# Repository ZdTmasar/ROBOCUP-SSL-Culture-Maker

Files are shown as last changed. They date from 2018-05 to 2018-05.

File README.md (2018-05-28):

# ROBOCUP-SSL-Culture-Maker
This is the work of LOO Darren, LAKHAL Nada, SEHOUBO Victoire and SALIBA Thomas for Rhoban SSL team

You will find a report on the repository explaining everything done during the project.

Basically there is :
-> How to make an identification of a motor
-> How to calculate a PID corrector
-> How to implemente the corrector
-> How to build a TestBench for a motor

If you are intersted in the SSL and more particularly with Rhoban, be sure to contact them. The remaining of the code is with them !

If you have any problem or questions about our work, be sure to contact us ;)

You will find the work of LAKHAL Nada and  SEHOUBO Victoire at the following google drive :

https://drive.google.com/drive/folders/1fRvp3v9pUFU8v6p59sLrBkBSSc9Q6jl7?usp=sharing

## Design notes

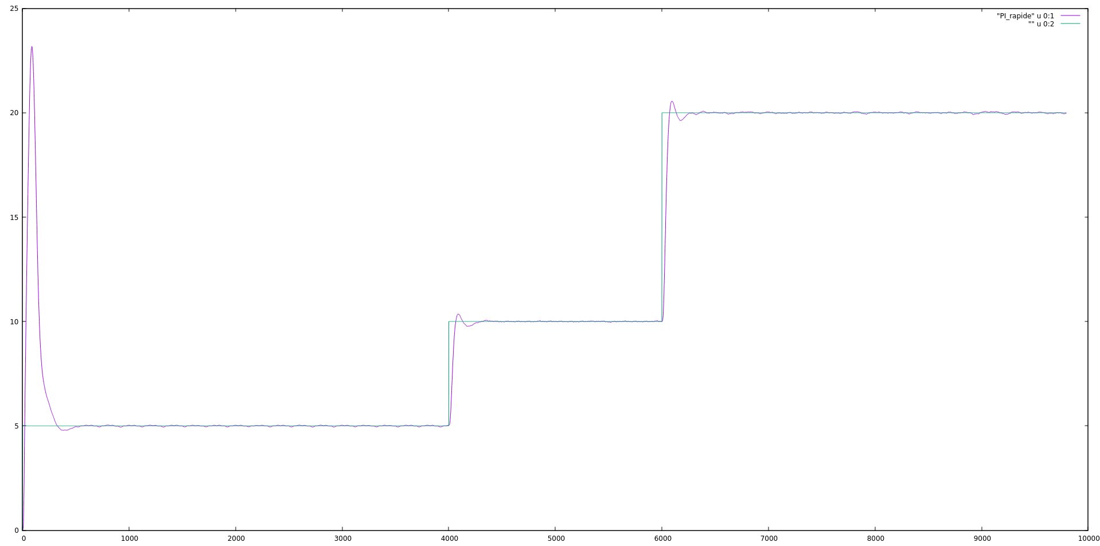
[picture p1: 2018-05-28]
Curves/Pi_rapide.png

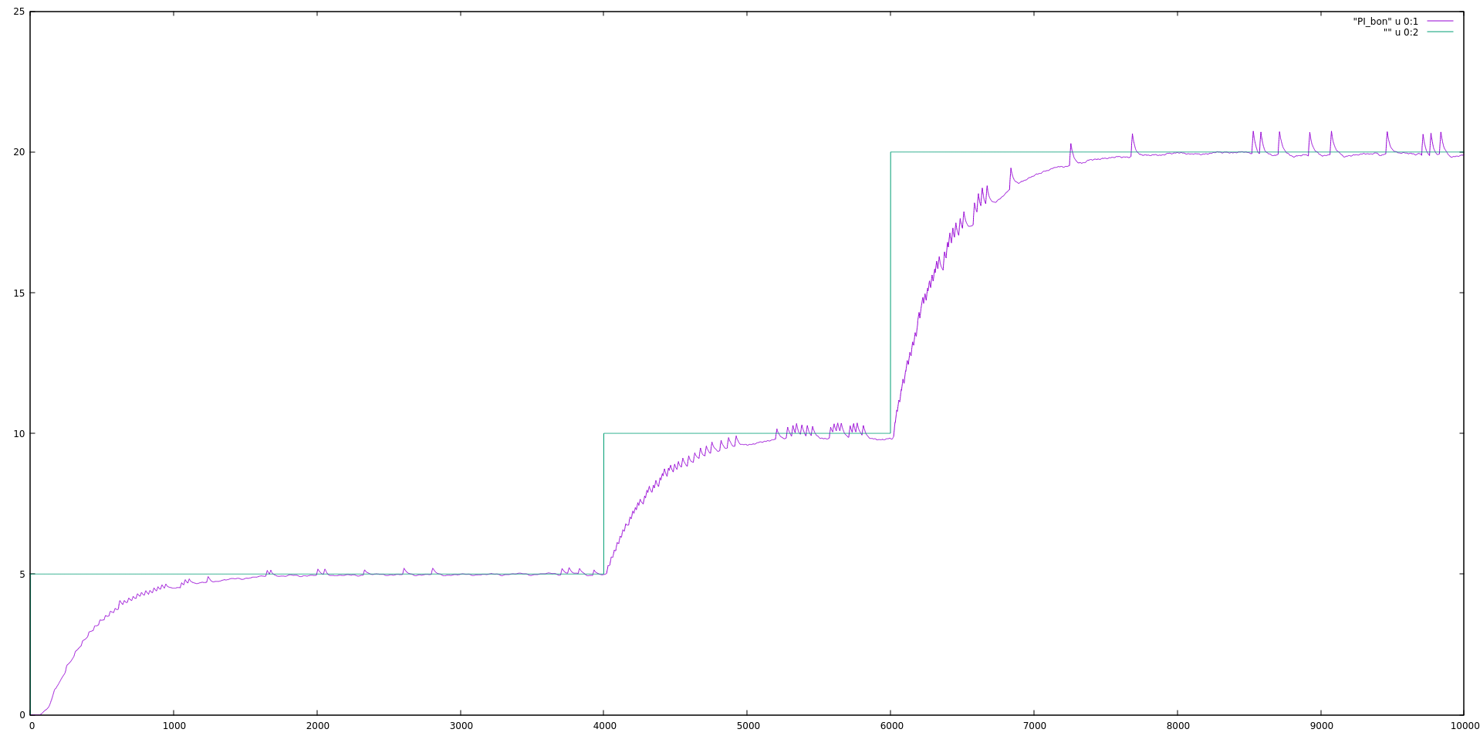
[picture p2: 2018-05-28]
Curves/PI_bon_arrache.png

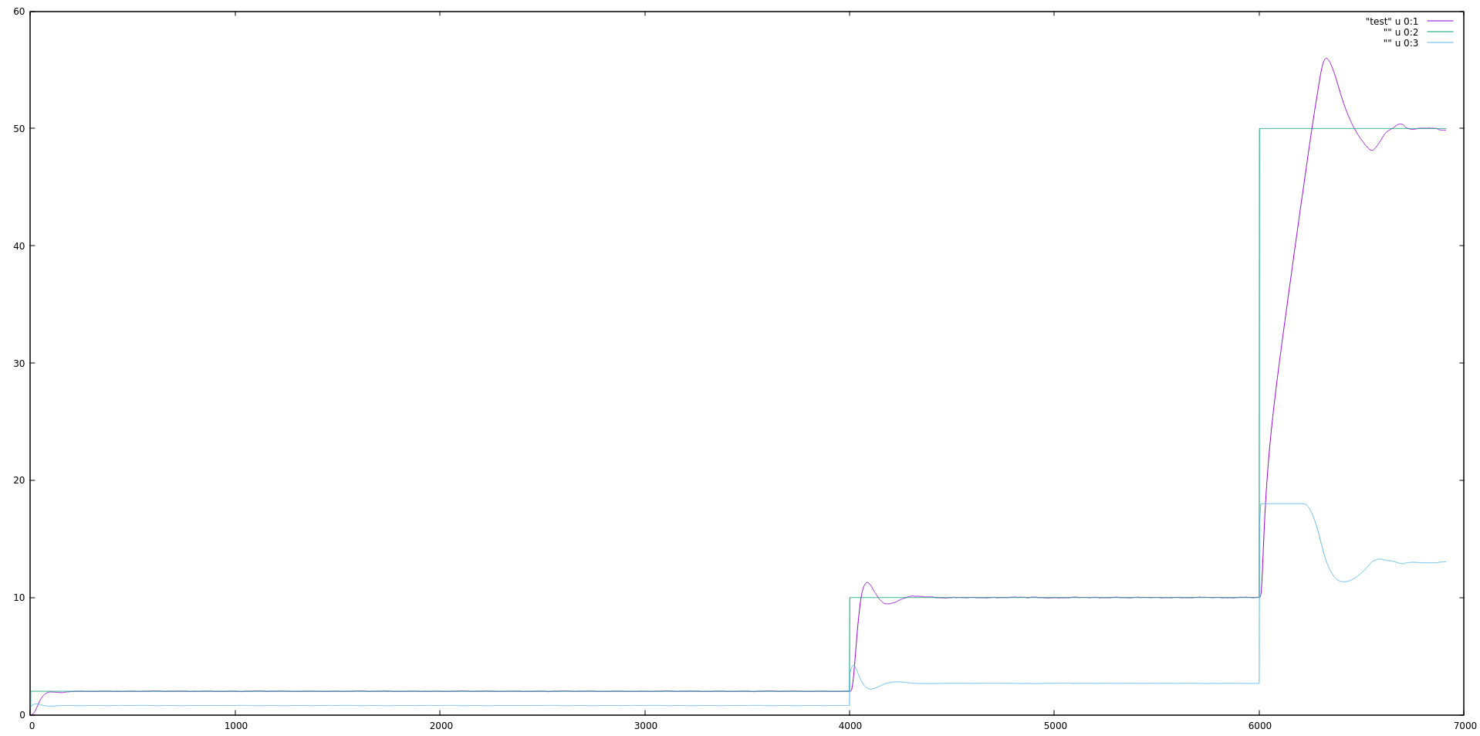
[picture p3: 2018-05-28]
Curves/PI_piffé_0.0536_-0.523.png

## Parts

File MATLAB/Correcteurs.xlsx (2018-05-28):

Ordre Procédé | Correcteur | wu | wi | Tr5% | 1er Dépassement | Coefficient Commande | Coefficient Erreur | Date | Commentaire | Tension moteur
2 | FPI | 20 | wu | 0,165 s | 8.75% | [1] | [0,0512; -0,0502] | 2018-04-13 | Pas trop mal mais plus lent que FPI2 | 20V
2 | FPI2 | 20 | wu | 0,163 s | 5% | [1] | [0,0524; -0,0514] | 2018-04-13 | Pas trop mal | 20V
1 | Caca | 20 | wu/2 | 0,408 s | 0 | [1] | [0,0356; -0,0352] | 2018-04-27 | Peut-être un peu trop lent | 20V
2 | Caca2 | 20 | wu/2 | 0,290 s | 0 | [1] | [0,0660; -0,0653] | 2018-04-27 | On a des possibilités | 20V
1 | Moto1 | 20 | 1,5*wu | 0,176 s | 6.25% | [1] | [0.0223; -0.0216] | 2018-04-27 | Un peu petit | 20V
2 | Moto2 | 20 | 1,5*wu |  |  | [1] | [0.0413; -0.0401] | 2018-04-27
1 | Moto1 Co+ | 20 | 1,5*wu |  |  | [1] | [0.0254; -0.0246] | 2018-04-27
 | A la main |  | 0,223 s | 16.25% | [1] | [0,0536; -0,0523] | 2018-05-03 | Plus lent que FPI et double dépassement | 24V
1 | Moto1 Co++ = 0,0440 | 20 | wu |  |  | [1] | [0.0444; -0.0436] | 2018-05-03
 |  |  |  |  | [1 -2.8971 2.7950 -0.8979] | [0.0014 -0.0013 -0.0014 0.0013]

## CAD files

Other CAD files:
TestBench_Inventor/Aimant_tenir.ipt
TestBench_Inventor/Brushless_70W.ipt
TestBench_Inventor/OldVersions/Aimant_tenir.0001.ipt
TestBench_Inventor/OldVersions/Brushless_70W.0001.ipt
TestBench_Inventor/OldVersions/Socle_Testbench.0006.ipt
TestBench_Inventor/OldVersions/Support_Carte.0017.ipt
TestBench_Inventor/OldVersions/Support_carte_ground.0003.ipt
TestBench_Inventor/OldVersions/Support_motor_front.0009.ipt
TestBench_Inventor/OldVersions/Support_motor_front_2.0001.ipt
TestBench_Inventor/OldVersions/Support_motor_front_ground.0007.ipt
TestBench_Inventor/OldVersions/TestBench.0009.iam
TestBench_Inventor/Socle_Testbench.ipt
TestBench_Inventor/Support_Carte.ipt
TestBench_Inventor/Support_carte_ground.ipt
TestBench_Inventor/Support_motor_back.ipt
TestBench_Inventor/Support_motor_front.ipt
TestBench_Inventor/Support_motor_front_2.ipt
TestBench_Inventor/Support_motor_front_ground.ipt
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

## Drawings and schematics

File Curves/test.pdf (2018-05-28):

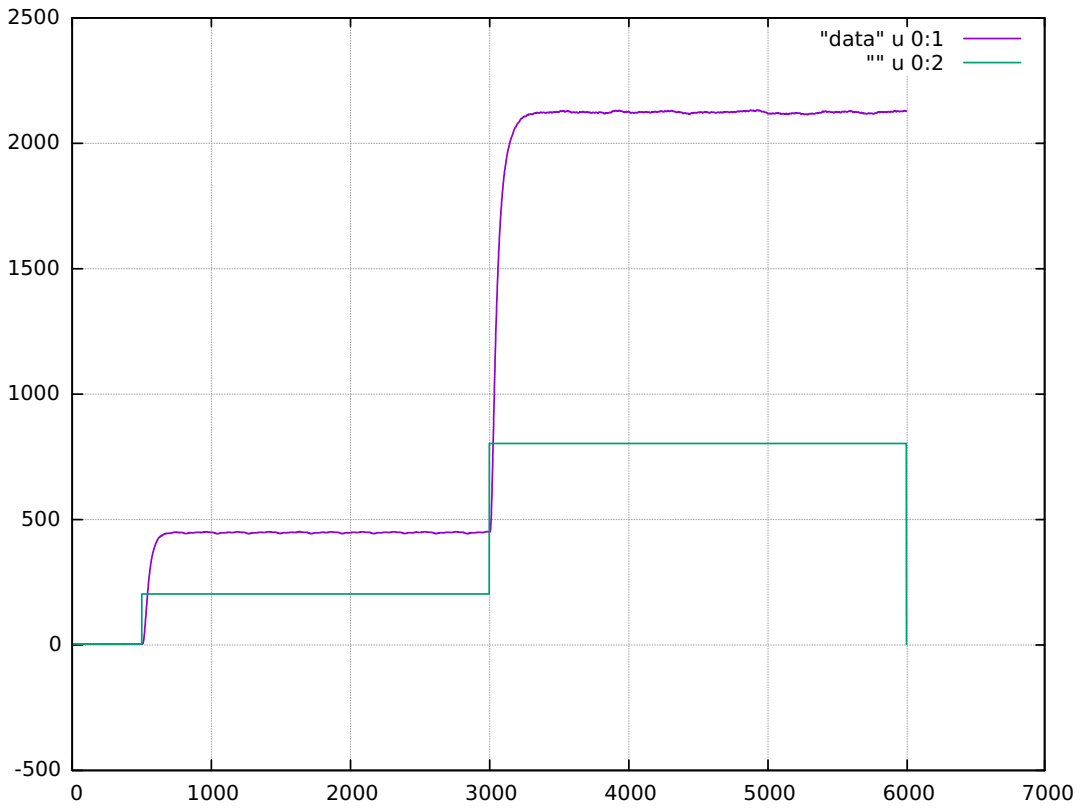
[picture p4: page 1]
"data" u 0:1 "" u 0:2

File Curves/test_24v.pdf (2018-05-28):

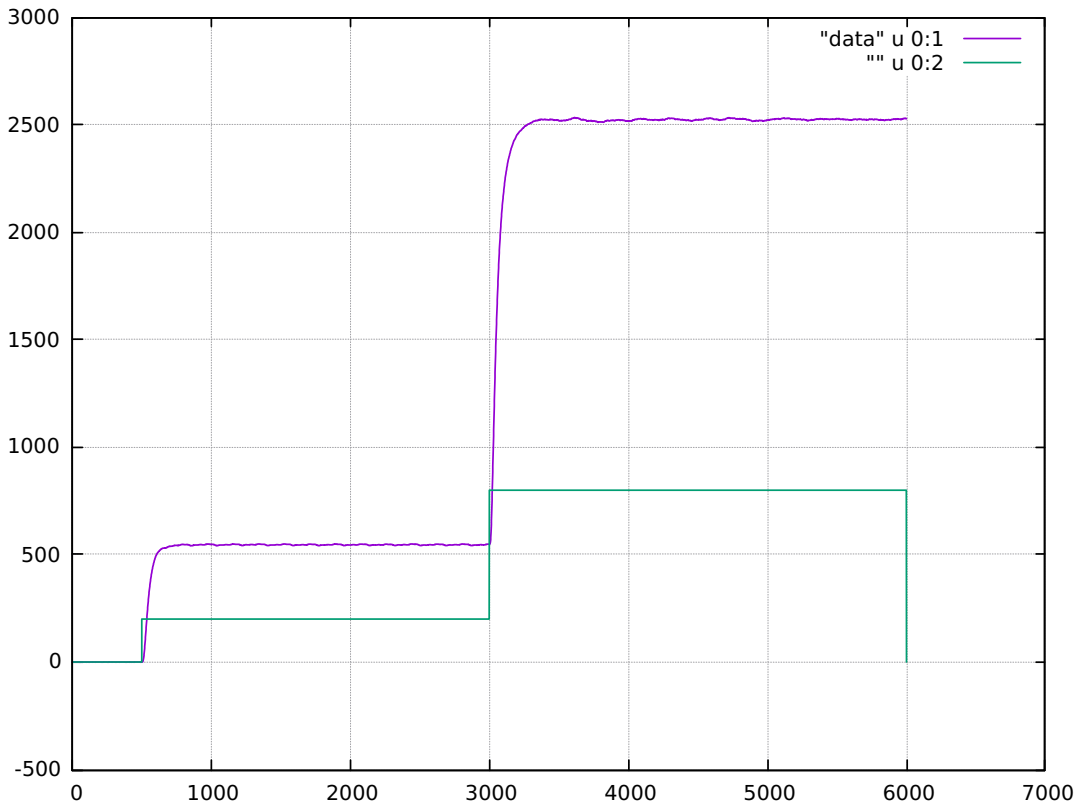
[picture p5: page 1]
"data" u 0:1 "" u 0:2

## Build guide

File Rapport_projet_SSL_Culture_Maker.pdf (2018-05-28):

# ROBOCUP SSL

## - PREMISSES A L’ASSERVISSEMENT D’UN ROBOT HOLONOME -

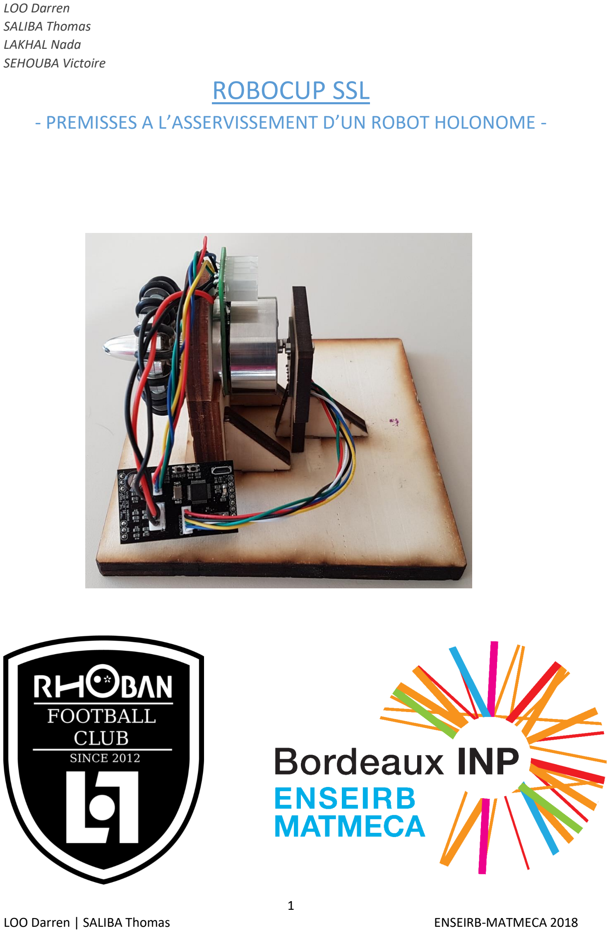
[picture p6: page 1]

LOO Darren | SALIBA Thomas | ENSEIRB-MATMECA 2018

LOO Darren
SALIBA Thomas
LAKHAL Nada
SEHOUBA Victoire

## SOMMAIRE

## Contexte

La Robocup est l’une des compétitions de robotique la plus connue dans le monde. Elle regroupe plusieurs catégories : Robocup Soccer (SSL, MSL, Humanoid, etc..), Robocup Rescue, Robocup @Home, Robocup Industrial et Robocup Junior. La catégorie qui nous intéresse ici est la SSL (Small Size League) de la Robocup Soccer.
Le principe est de se faire affronter deux équipes de six robots à roues qui sont pour la plupart holonomes dans un match de football. Les défis sont donc d’arriver à faire un robot maniable, précis et rapide mais sans qu’il soit incontrôlable. L’objectif de ce livret est de démarrer l’implémentation d’un asservissement d’un robot SSL par une approche rigoureuse et méthodologique de l’automatique. Ce livret contient donc les parties suivantes :
➔ Décomposition du robot
➔ Création d’un TestBench
➔ Identification d’un moteur seul
➔ Asservissement d’un moteur seul ➔ Identification d’un moteur in situ
➔ Asservissement d’un moteur in situ

Chaque partie sera introduite et expliquée de manière simple et didactique. Cependant certaines explications seront succinctes car il existe des documents qui approfondissent beaucoup mieux le propos (Voir Bibliographie pour plus de détails). L’étude se fera sur un robot holonome de l’équipe Rhoban utilisant 4 moteurs brushless Maxon EC 45 flat en Direct Driving.

## Décomposition du robot

Pour contrôler parfaitement un robot, il faut le connaître, c’est-à-dire identifier son comportement par rapport à certaines commandes. Cette phase, l’identification, doit être faite plusieurs fois à différents niveaux : une roue, toutes les roues ensemble puis le robot entier.
Dans un premier temps, il est nécessaire de pouvoir contrôler correctement chaque moteur. Pour cela, il faut effectuer une identification du moteur : il faut caractériser son comportement et sa réponse à une commande. Pour cela, un banc de test a été conçu pour accueillir un moteur et effectuer des tests plus facilement. Dans cette première version, le moteur tourne avec une roue holonome : il n’y a que la charge de la roue sur l’axe du moteur.
Une fois que le moteur a été identifié, que son comportement a été caractérisé, que son modèle de comportement a été établi, il devient possible de synthétiser un correcteur qui permettra d’obtenir du moteur une vitesse souhaitée et ce quel que soit les perturbations. On obtient donc la chaine suivante :

Figure 1 : Schéma bloc d’une chaîne asservie

G représentant le comportement du moteur sous forme de fonction de transfert (vitesse de rotation/tension appliquée), et C le correcteur que l’on synthétisera par la suite. Il est à noter que le retour sur la vitesse de la roue provient d’un encodeur magnétique captant le champ tournant d’un aimant fixé à l’arrière du moteur brushless.
Une fois cette chaîne implémentée et validée, on peut se concentrer sur un autre banc de test qui met en situation le moteur avec un certain poids appliqué en sa surface. L’idée est de refaire l’identification du moteur avec les contraintes qu’il aurait sur le robot. La chaine précédente est surtout pour valider tous les éléments nécessaires : le capteur, le calcul, l’implémentation. Car une fois tout ceci validé, refaire une identification et la mettre en place est très simple.
Maintenant, chaque processus va être détaillé.

## Conception du premier banc de test

Il y a plusieurs manières d’effectuer un banc de test. Ce qui sera décrit par la suite se rapproche de ce qui a semblé être le plus simple à mettre en œuvre.
Les contraintes qui ont été fixées sont les suivantes :
-le moteur doit être soutenu dans son intégralité ;
-la roue ne doit pas toucher le sol ;
-l’ensemble doit être stable lors des tests ;
-il faut que l’encodeur magnétique soit parfaitement en vis-à-vis de l’aimant.
En effet, il faut un maximum de stabilité pour éviter que des perturbations viennent altérer les mesures. Le placement de l’encodeur magnétique est très important car c’est lui qui effectue les mesures sur lesquelles tout l’asservissement se base.
Globalement, le banc de test est composé de 5 pièces différentes. Toutes les pièces ont été conçues avec le logiciel Autodesk Inventor et ont été faite par découpage laser sur bois.

### Concevoir une pièce

La conception d’une pièce est séquentielle. En effet, on ne peut généralement travailler que sur une surface à la fois. Il faut donc avoir une bonne idée des objectifs que la pièce devra remplir. Des ébauches au crayon sont toujours un bon début. Dans notre cas, puisque les pièces seront faîtes par découpage laser, il n’y aura qu’une face à faire. Toutefois, la démarche peut être réitérée autant de fois que possible pour effectuer des pièces plus compliquées. Dans tous les cas, il faut toujours garder à l’esprit le moyen qui sera utilisé pour fabriquer la pièce (découpage, impression 3D, pliage, emboutissage, usinage etc…), certaines formes étant impossible à réaliser selon le procédé d’usinage retenu.
Dans notre cas, les 5 pièces sont :
- le socle du banc de test ;
- un support pour le moteur ;
- un support pour la carte de l’encodeur ;
- des soutiens pour les supports (2 identiques pour le moteur et 1 pour la carte) ;

### Dessiner une face

Pour dessiner une face plane, il faut créer une esquisse. Dans un premier temps, dans le volet de navigation du modèle, sélectionner un plan qui servira de référence à l’esquisse. Puis créer une esquisse. Le logiciel propose plusieurs fonctions qui permettent de créer des formes géométriques simples. L’outil « Ajuster » (icône de ciseaux) permet de supprimer des portions de trait non désirées. Pour fixer des éléments par rapport à d’autres, il faut utiliser des contraintes. Il y a plusieurs types de contraintes : de dimensions (qu’on appelle des côtes), de positionnement (coïncidence de points, colinéarités d’axes ou parallélisme…). Lorsqu’un élément est totalement contraint, il apparaît en bleu sur l’esquisse, les éléments non contraints étant en vert. Contraindre totalement une esquisse a plusieurs avantages. Dans un premier temps, cela permet de maîtriser totalement les dimensions / orientations que prendra la pièce. De plus, si une esquisse est bien contrainte, il est aisé d’en changer les dimensions sans que cela ait d’impact néfaste sur tout le travail qui sera effectué après et qui se base sur l’esquisse même. Aussi, cela permet à un tiers de voir clairement les relations qu’il peut y avoir entre les éléments ne laissant plus aucune place au doute.
Enfin, une fois que l’esquisse est réalisée et prête, il est possible de l’extruder : de l’utiliser pour créer de la matière ou encore de l’utiliser pour enlever de la matière (sur une pièce déjà existante par exemple). Dans notre cas, une extrusion de 10mm a été effectuée sur toutes les pièces. En effet, les planches de bois qui passeront au découpage sont d’épaisseur 10mm.

### Assembler les pièces

Une fois que toutes les pièces ont été réalisées, il est possible de les assembler afin d’avoir un bon aperçu du montage final.
Il faut créer un fichier de type « Ensemble » et y placer les différentes pièces qui ont été faites. Pour des raisons pratiques, il est préférable de commencer par la pièce centrale du montage. Puis, il faut bloquer la pièce dans l’espace pour inhiber ses déplacements. Ensuite il faut rajouter les autres pièces. Pour placer une pièce, il faut aussi lui imposer des contraintes, de position (distance, colinéarité…) et de surface (placage en vis-à-vis ou affleurement etc…).
Pour qu’une pièce fixe soit bien contrainte, il faut lui retirer ses 6 degrés de liberté dans l’espace (3 translations sur les axes du repère et 3 rotations autour de ces axes). Si une pièce est mobile, il faut bien sûr lui laisser les degrés de liberté nécessaires.
Afin de vérifier qu’un assemblage se passe sans accroc, il est possible de changer le style visuel des pièces. Le paramètre « Filaire avec arêtes masquées » est plutôt bon pour cette tâche. Le logiciel n’informe pas lorsque deux pièces se superposent.

### Découpage des pièces

Pour passer à la découpeuse laser, il faut exporter les faces de chaque pièce en format .dxf. Puis les ouvrir et les réenregistrer avec le logiciel QCad. Il faut ensuite les ouvrir avec Inkscape, tout sélectionner, tout dégrouper et appliquer les bons paramètres pour la découpe sur les contours et les fonds. Il ne reste plus qu’à laisser faire la machine et assembler les pièces.

## Première identification du moteur

### Principe

Le concept est de cette phase est donc de caractériser le comportement moteur. Pour cela il existe plusieurs approches : par représentation d’états ou par fonction de transfert. La première méthode consiste, à partir des équations différentielles régissant un moteur, à dresser un modèle basé sur des états (internes ou non) du système, représenté par des matrices. Cependant, cette méthode est compliquée à appréhender et l’implémentation numérique est plus complexe qu’à partir d’une fonction de transfert. La deuxième méthode, celle utilisée ici, consiste à modéliser le moteur par une fonction de transfert (domaine fréquentiel). On va donc exciter le moteur en lui appliquant une tension en entrée et observer sa réponse.
L’excitation la plus réputée est l’application d’un échelon. De fait, fréquentiellement, l’échelon comporte une richesse fréquentielle ce qui fait que l’on va pouvoir observer plusieurs choses :
➔ Le dépassement
➔ L’erreur statique
➔ Le gain statique
➔ Le temps de montée
➔ La pseudo-pulsation
➔ Etc…
Ces facteurs-là sont plus ou moins observables selon la forme de la réponse du moteur. La fonction de transfert a souvent la forme suivante :

G(p) =

Gain statique
(1 +

p
wc1

) (1 +

p
wc2

) (1 +

p
wc2

) …

p étant jw avec j l’imaginaire et w la pulsation et wc les pulsations de coupures.

Dans la vie réelle, la plupart des systèmes sont des filtres de type passe-bas d’où la présence de pôles et non de zéros dans la fonction de transfert. Les pulsations de coupures représentent des fréquences caractéristiques du système étudié. On les retrouve grâce à l’identification. On peut également les retrouver leur expression analytique en passant par les équations théoriques.
Dans le modèle d’un moteur, il existe deux pulsations de coupures : la coupure mécanique et la coupure électrique. La première est due à tous les frottements et les inerties mécaniques présentes sur le moteur et la deuxième à la bobine et résistance du moteur. Généralement, la deuxième pulsation étant très grande devant la première, on a tendances à la négliger car le gain aux fréquences élevées est si bas que cette caractéristique est négligeable. On se retrouve donc souvent avec une fonction d’ordre 1.
Dans la partie suivante, il sera montré comment a été identifié le moteur.

### Mesures

La première étape est l’observation de la réponse du système à une consigne. Pour cela, il faut récupérer à la fois les mesures de vitesse de rotation du moteur, la commande qui lui a été envoyé et traiter ces données (mise en forme et exploitation). Toute cette partie est compilée dans un script Matlab.
Les données relatives à la vitesse de rotation du moteur sont exprimées en centième de tour par seconde. Elles doivent être converties en rad/s. Aussi, les données relatives à la commande sont proportionnelles à cette dernière. Avant de pouvoir les exploiter correctement, il faut les ramener à des unités conventionnelles : rad/s pour la vitesse de rotation et V pour la commande.
Une série de deux échelons est envoyée au moteur afin de ne pas prendre dans les mesures les effets des frottements secs et autres perturbations agissant sur le moteur au démarrage.
Le second échelon correspond à une variation de PWM de 200 à 800 envoyée au moteur. Cela correspond à une variation de la tension de commande de 1.6V à 6.4V.

Un premier tracé des données est effectué. Il permet dans un premier temps de choisir le modèle qui servira à l’identification du procédé, puis dans un second temps de définir les plages de données qui seront utilisées pour déterminer les éléments du modèle. En effet, un léger bruit interfère avec les données mesurées. Puisqu’en régime permanent la vitesse du moteur devrait être constante, une moyenne est effectuée sur beaucoup de points afin de diminuer les effets du bruit.

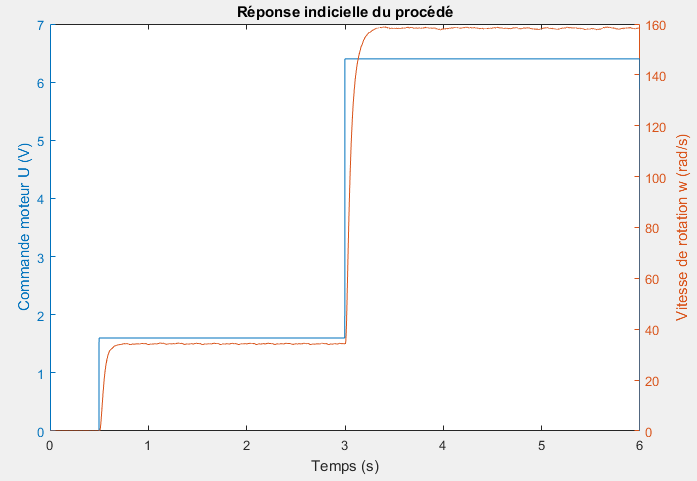
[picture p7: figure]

Figure 2 : Réponse indicielle du procédé – Tracé préliminaire

D’après l’allure de la courbe représentant la vitesse de rotation du moteur par rapport au temps, il est possible de modéliser le procédé par un système du second ordre apériodique (très amorti). En effet, elle s’apparente fortement à l’allure de la réponse indicielle d’un système du premier ordre (pas de dépassement de la valeur finale) toutefois, la pente à l’origine (ici 3s, origine du second échelon) n’est pas nulle. On en déduit la forme de la fonction de transfert du procédé suivante : G(p) =

K0
(1+τ1p)(1+τ2p)

,
K0 étant le gain statique, τ1 et τ2 les constantes de temps associées aux pulsations de coupure du procédé.

On mesure K0 = 25.8532. Cela nous permet de tracer l’image en tension de la vitesse de rotation du moteur afin de l’avoir sur la même échelle que la tension de commande du moteur. Cette mise à l’échelle est nécessaire pour pouvoir mettre en œuvre la méthode des tangentes et obtenir les valeurs des constantes de temps.
En plaçant la tangente au point d’inflexion de la courbe, on a τ1 à l’intersection de cette dernière et de la droite y = 1.6 (valeur de l’échelon bas). De plus, l’intersection entre cette tangente et la valeur finale du procédé donne τ1 + τ2 . On a finalement τ1 = 11ms et τ2 = 78ms qui correspondent respectivement à des pulsations de coupure de 90.9 rad/s et 12,8 rad/s.

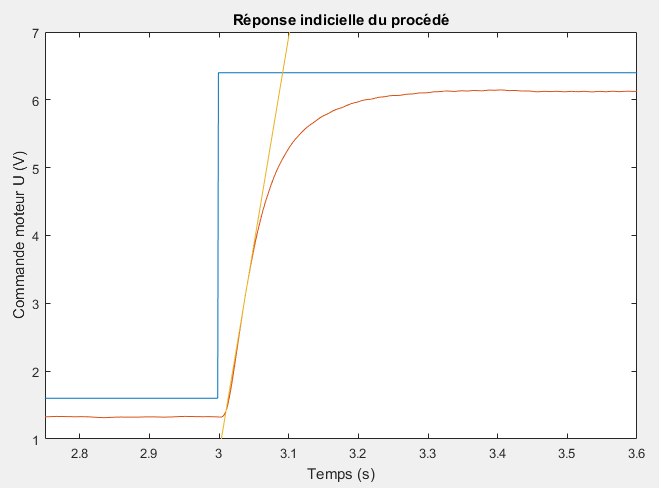
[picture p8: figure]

Figure 3 : Réponse indicielle du procédé

Finalement, le procédé est modélisé par la fonction de transfert :

G(p) =

25.8532
(1 + 0.011p)(1 + 0.078p)

## Calcul du premier correcteur

### Principe

Le correcteur peut également être représenté par une fonction de transfert qui représente la tension à appliquer au moteur en fonction de l’erreur qu’il y a entre la consigne de vitesse et la vitesse réelle du moteur. Cette fonction de transfert se base sur la connaissance du moteur (identification). Le concept est de choisir une pulsation à laquelle l’on compte effectuer la commande. Généralement, on prend cette pulsation plus grande que la dernière fréquence de coupure. On va alors fixer le gain à 1 à cette fréquence et on va étudier la phase du procédé.
De fait, on désire que le correcteur suivi du procédé soit stable et rapide selon un cahier des charges. Pour cela, on identifie le point de non stabilité : la pulsation à laquelle le gain de la fonction de transfert en Boucle Ouverte (FTBO = correcteur * procédé) vaut 0dB et sa marge de phase. C’est-à-dire la différence entre sa phase et -180°. De fait, plus on est proche de -180° plus on se rapproche de l’instabilité. On cherche alors avec le correcteur à décaler la réponse fréquentielle au-dessus de -180°, au moins pour les gains forts. C’est pour cela que l’on fixe généralement la marge de phase à 55° environ à la fréquence de travail : cela favorise une réponse rapide et une stabilité correcte.
Dans la partie qui suit, il sera montré comment on arrive à faire ces calculs à l’aide de Matlab.

### Synthèse du régulateur avec Matlab

La première étape est de définir le procédé à réguler et les conditions que l’on souhaite remplir. Dans notre cas, un simple correcteur à actions proportionnelle et intégrale a été synthétisé. En effet, le système étant déjà très amorti (réponse indicielle d’un second ordre amorti), un apport de phase par une action dérivée n’est pas nécessaire. Le régulateur aura donc la forme suivante :

C(p) = C0

1 +

p
ωi
p
ωi
La pulsation au gain unité sera imposée à 20 rad/s et sera la même que la pulsation de la partie intégrale du régulateur ωi
Le gain C0 servira à ajuster la réponse du système en boucle ouverte afin d’assurer un gain nul

à 20 rad/s. On a donc K0C0

ωi
ωu

√1 + (
ωu
ωi

)² = 1 soit C0 =

ωu
ωi

1
K0√1+(
ωu
ωi

)²

Finalement, le régulateur à actions proportionnelle et intégrale s’écrit :

C(p) = 0.0519

1 +

p
20
p
20

### Simulations

Afin de vérifier que le régulateur synthétisé respecte bien le cahier des charges qui a été fixé, différentes simulations sont effectuées dans les domaines temporel et fréquentiel.

Dans un premier temps la réponse indicielle du procédé identifié précédemment et ses diagrammes de Bode sont observés.

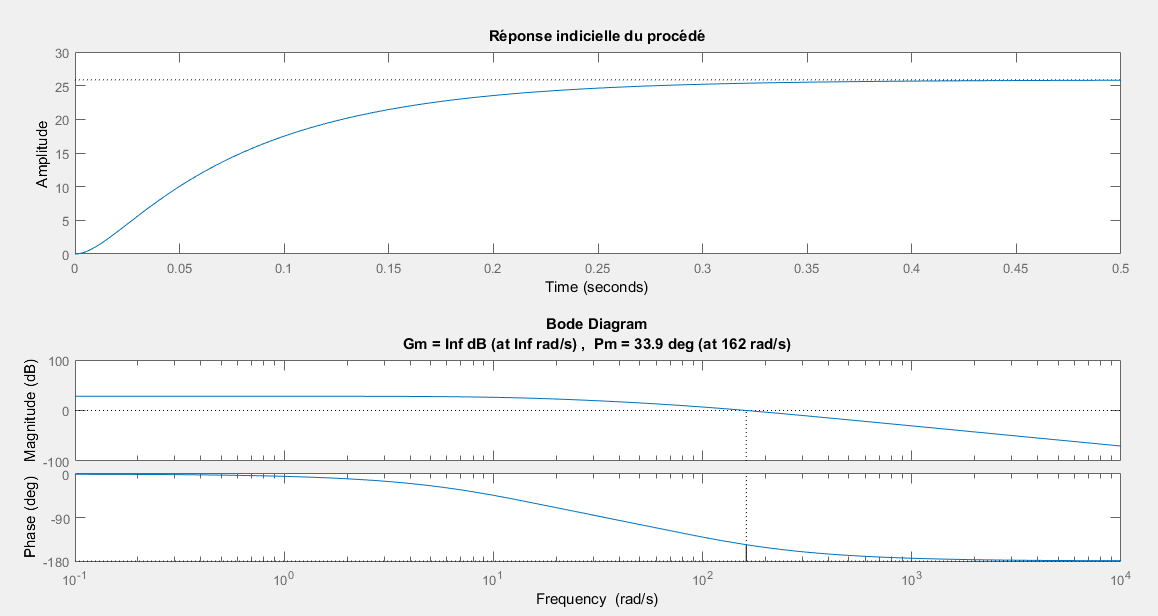
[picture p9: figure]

Figure 4 : Réponse indicielle et diagrammes de Bode du procédé

La simulation de la réponse indicielle du procédé permet d’effectuer une comparaison avec la courbe qui avait servi à l’identification. Globalement, cela permet de vérifier que le modèle qui a été identifié est proche de la réalité.
Puis, les tracés des diagrammes de Bode nous informent du comportement fréquentiel du modèle. On va chercher à améliorer la marge de phase afin d’augmenter le degré de stabilité du système en ajoutant un régulateur.

Il est aussi possible d’observer la réponse indicielle du régulateur et ses diagrammes de Bode.

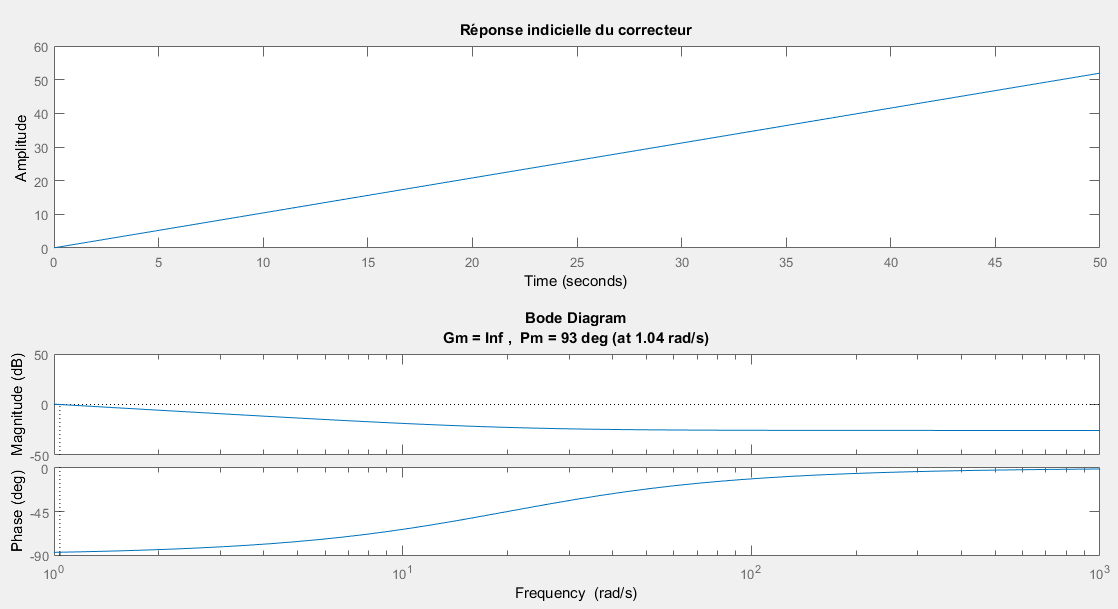
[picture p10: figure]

Figure 5 : Réponse indicielle et diagrammes de Bode du régulateur

Le régulateur étant à action proportionnelle et intégrale, une augmentation progressive (accumulation) est observée sur la réponse indicielle. Elle est due à l’action intégrale qui va permettre d’annuler l’erreur statique du moteur. La précision du système sera donc parfaite pour une consigne en échelon.

Tracer les diagrammes de Bode de la fonction de transfert en boucle ouverte permet de nous assurer que le cahier des charges qui a été fixé est bien respecté et donc que le régulateur ait été synthétisé correctement. En effet, comme le montre la figure suivante, la pulsation au gain unité est bien à 20 rad/s et la marge de phase est de 65,3° ce qui assure une bonne stabilité du système.

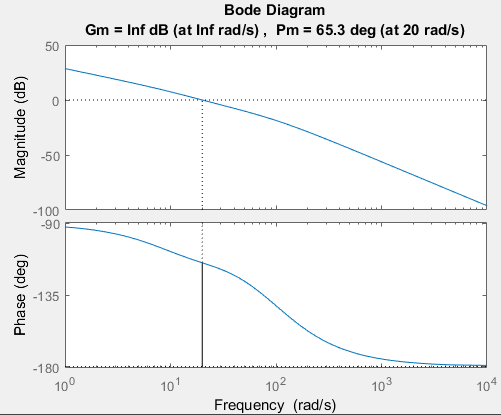
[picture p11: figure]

Figure 6 : Diagrammes de Bode de la fonction de transfert en boucle ouverte de l’asservissement

Il est maintenant intéressant d’observer la réponse indicielle de la fonction de transfert en boucle fermée, soit la réponse du procédé asservi, sur la figure suivante.
On y relève les caractéristiques suivantes :
-une absence d’erreur statique ;
-un dépassement de la valeur final inférieur à 10% ;
-un temps de réponse à 5% de 0.213s ;
-une constante de temps de 0.0526s.

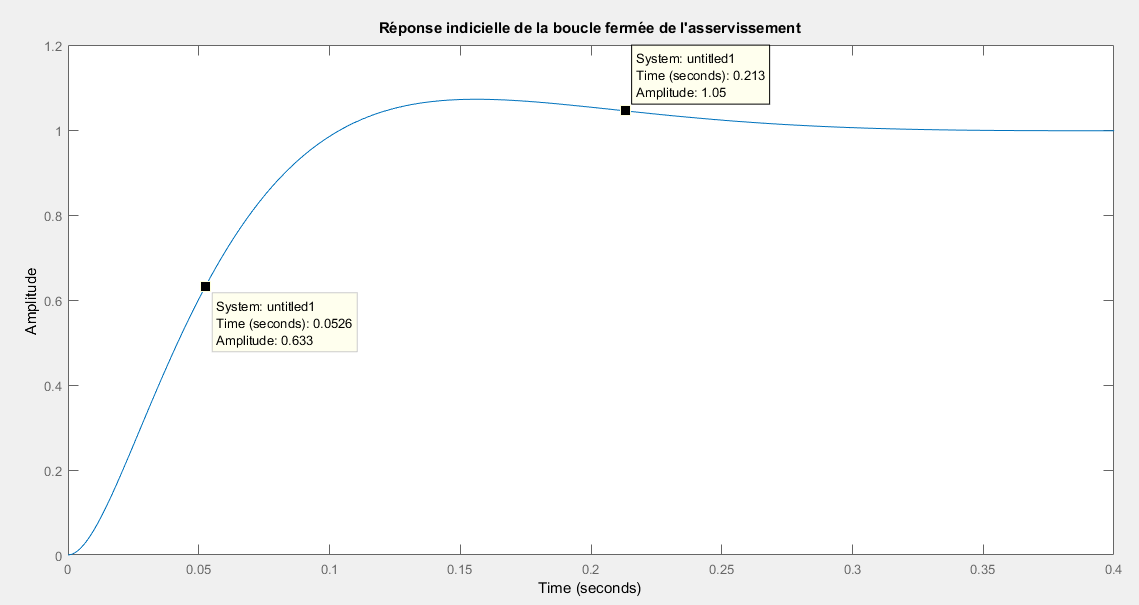
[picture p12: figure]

Figure 7 : Réponse indicielle de la fonction de transfert en boucle fermée de l’asservissement

### Passage en numérique

La question que l’on peut se poser est comment implanter ce correcteur sur un processeur qui ne connait pas le domaine continu. De fait, cela ne semble pas naturel mais il existe plusieurs moyens : l’approximation en Delta et la transformée bilinéaire. Cependant les deux sont basés à un moment ou à un autre sur la transformé en z. L’approximation en Delta est valable uniquement si la fréquence d’échantillonnage est suffisamment grande devant les autres fréquences du procédé (x10 minimum). Alors il suffit de remplacer la variable p de la fonction de transfert par :
p →

1− z

−1
Te

, avec Te la période d’échantillonnage La période d’échantillonnage est très importante à prendre en compte. Premièrement elle doit être plus grande que la fréquence de travail. Il faut au moins respecter le théorème de Shannon (x2 la fréquence de travail) mais en pratique, il est conseillé de la prendre au moins à x10. Cela permet notamment d’avoir une image du signal mesuré pertinente vis-à-vis de la dynamique du système Dans notre cas, l’échantillonnage est à 1kHz. Cela correspond à la fréquence la plus limitante de tout notre système (capteur inclus). De fait, le capteur, une fois traitée numériquement, renvoi une valeur de vitesse instantanée viable toutes les millisecondes. Généralement, cette fréquence tourne entre quelques Hz et 1kHz pour contrôler un robot.
Une fois la transformation faite (la fonction s’appelle c2d() sur Matlab en prenant comme paramètre ‘zoh’), on obtient une fonction de transfert en fonction de z qu’il faut passer en fonction de transfert en fonction de la variable z⁻¹
, correspondant en fait à l’opérateur retard. Une fois la fonction de transfert obtenu, on exécute le raisonnement suivant.
La fonction de transfert du correcteur étant U(p)
ε(p)

avec U(p) la commande et ε(p) l’erreur, en considérant les coefficients précédents on obtient le passage suivant :

U(p)
ε(p)

=

α1 + α2z

−1 + α3z

−2 …
1 + β1z

−1 + β2z

−2 …

→ u[n] = −β1 ∗ u[n − 1] − β2 ∗ [n − 2] + α1 ∗ ε[n] + α2 ∗ ε[n − 1] + α3 ∗ ε[n − 2]

n représente l’instant actuel et n-1 l’instant précédent, etc… Ainsi on voit que la commande à chaque instant est déterminée par une combinaison linéaire des commandes précédentes et des erreurs actuelles et précédentes. C’est cette équation qui est implémentée dans le processeur et qui est itérée à la fréquence d’échantillonnage. Il faut donc à chaque instant garder en mémoire les commandes et les erreurs dans des FIFO de la taille du nombre de coefficients présents. Dans la partie suivante, nous allons voir comment nous avons implémenté cela dans le firmware développé par Rhoban.

## Utilisation du Software et implémentation du correcteur

Le firmware par Rhoban étant assez étendu est complexe, pour notre partie il n’était pas nécessaire de tout comprendre. Nous nous sommes donc penchés sur les fichiers « servo.h », « servo.cpp », « motor.h » et « motor.cpp ». Dans ces fichiers il y a, entre autres, la réception de l’encodeur magnétique et le drive du pont en H qui alimente le moteur.
La version de servo.h est disponible sur le git associé. Les changements que nous avons effectués sont les suivants :
➔ Description d’une classe FIFO qui permettrait la mémorisation des commandes et des erreurs précédentes
➔ Implémentation des coefficients calculés
➔ Implémentation du debug afin de pouvoir visualiser les données à l’aide de gnuplot
➔ Implémentation d’une commande sur le terminal permettant d’envoyer un échelon de consigne.
Tout est assez clair sur le fichier. L’asservissement se déroule dans la condition « if servo_enable = true ; » et les paramètres sont situés surtout en haut du fichier.
Ci-dessous est présentée la démarche à suivre pour implémenter un nouveau firmware sur les brushless de Rhoban :
Dans un premier temps, cloner le git de Rhoban (s’ils vous l’autorisent évidemment). Ensuite, se placer dans le fichier brushless\firmware\. Ici se situent tous les fichiers présents sur le driver du moteur. Il suffit alors de modifier ce que l’on désire puis d’exécuter les commande « make » puis « make install » pour flasher le driver. Ensuite pour se connecter à la carte il faut taper la commande suivante : « cu -l \ttyACM0 » dans le terminal (Tout ceci sous Linux évidemment). Une fois connecté, voici les différentes commandes disponibles :
➔ pwm <valeur> : applique une pwm souhaitée (de 0 à 3000) au moteur sans passer par l’asservissement.
➔ set <valeur> : applique une consigne en tour/s à la boucle d’asservissement.
➔ step <valeur> : permet de donner une nouvelle consigne (tour/s) sans nettoyer les FIFOs de mémoires.
➔ fp=<phase> : force la pwm fixée dans uniquement une phase (allant de 0 à 5).
➔ sdb=1 : lance le programme d’identification définie dans servo.h. C’est une suite d’échelon avec visualisation de la vitesse et de la consigne.
➔ hall : visualise ce que renvoie le capteur à effet hall du brushless (codage de Gray).
➔ speed : visualise la vitesse instantanée du moteur.
➔ Et bien d’autres, il suffit de taper « help » pour avoir une liste plus complète. Dans une future mise à jour, ce tutoriel sera un peu plus développé et générique.

Voici finalement les performances que nous avons obtenues sur le moteur avec la roue uniquement :

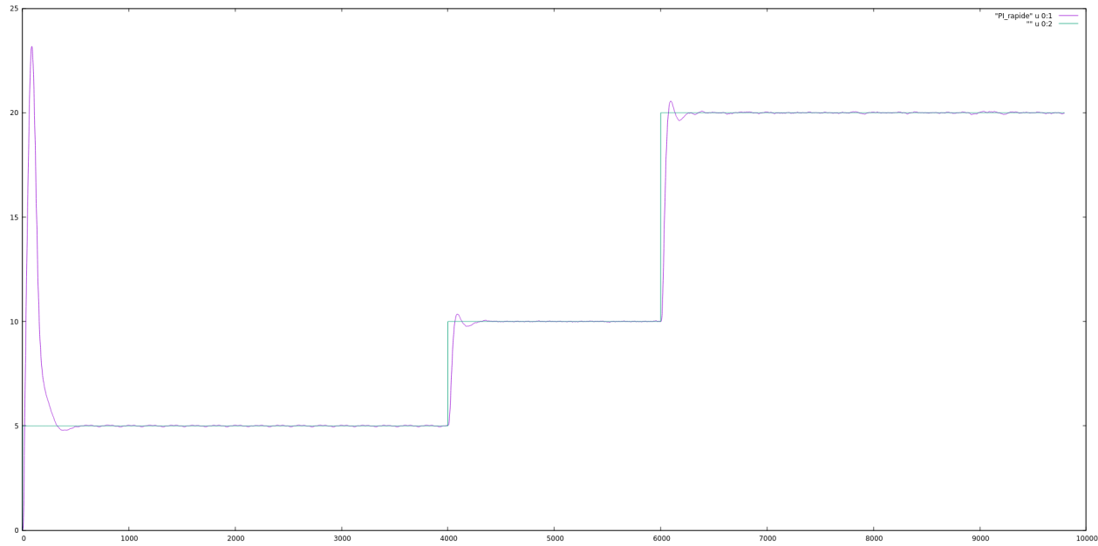
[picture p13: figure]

Figure 8 : Réponse du moteur à des échelons de 10 tours/secondes puis 20 tours/secondes

On observe que le moteur atteint la vitesse demandée en 0.2 secondes avec un léger dépassement. Le résultat est très satisfaisant. On en conclut que la chaîne de calcul et indentification est validée. Nous pouvons passer à l’étape d’au-dessus.

## Conception du second banc de test

Toujours avec l’objectif de s’approcher au maximum de la situation dans laquelle les moteurs vont fonctionner, un second banc de test a été réalisé. Les mêmes méthodes ont été utilisées que lors de la conception du premier banc de test. L’utilisation de la découpeuse laser permet en effet un prototypage rapide.
Ce banc de test aura pour objectif principal de permettre mettre en œuvre le comportement d’un moteur avec roue qui touche le sol. Des tests en conditions presque réelles sont souhaités. Pour cela, la structure du banc ne sera pas statique comme précédemment mais dynamique. Le moteur entraînera son support avec lui autour d’un axe vertical. Une charge pourra être rajoutée sur l’ensemble et représentera l’effet d’un quart du poids du robot. On suppose que les charges seront uniformément réparties sur les 4 moteurs en situation réelle. Il devient donc possible de prendre en compte les inerties relatives à la masse du robot.
En plus de pouvoir observer le comportement du moteur lorsqu’il est en mouvement, ce banc nous permet d’effectuer les mesures lors du démarrage du moteur sur le même sol qui recouvre les terrains. En effet, il ne faut pas négliger les frottements de la roue sur le sol lors de l’étude : sans frottement, il n’y a pas de déplacement. Cela met aussi en évidence le problème de glissement des roues. Le patinage des roues sur le terrain peut s’avérer problématique. L’utilisation du banc peut donc permettre de s’assurer de la plage de commande où il n’y aura pas de glissement des roues.

Un problème persiste toutefois : les roues étant holonomes, elles permettent aussi des déplacements selon les axes de rotation des moteurs. Mettre en place un banc simple qui permet d’effectuer des tests sur ces mouvements n’est pas une mince affaire. On ne les considérera donc pas ici mais des tests sur le fonctionnement d’un robot complet peuvent combler ce manque.

## Pour aller plus loin

### Deuxième identification du moteur

La prochaine étape serait de continuer sur le second banc moteur et d’effectuer une nouvelle identification du procédé. En effet, sur le premier banc, l’absence de charge et de frottements fait que le système était certainement plus rapide. Il serait intéressant de comparer les deux comportements du moteur (à vide et chargé).

### Synthèse et implantation d’un second correcteur

Si nous avions eu le temps, nous aurions synthétisé et implémenté le dernier correcteur avec le deuxième banc moteur afin de voir la différence d’efficacité sur le déplacement global. Il aurait été intéressant d’observer et de quantifier cette amélioration.

### Etude mécanique et dynamique

Rhoban avait déjà un robot complet avec un correcteur calculé empiriquement. Ils ont déjà effectué l’étude dynamique consistant à envoyer une commande de vitesse à chaque roue considérant la vitesse désirée du robot et sa rotation sur lui-même. Il est important d’effectuer cette étude si le désir est de concevoir un robot holonome.

### Suppression des « saut » dû aux roues holonomes

Comme il est possible de le voir sur les photos, une roue holonome est assez particulière. Celle-ci surtout possèdes des roues radiales assez longue et donc aux basses vitesses, le robot tend à vibrer car il passe d’une roue radiale à l’autre. L’idée de cette amélioration serait d’anticiper ces passages là en fonction de la position de la roue. Il faudrait donc superposer à l’asservissement de base une compensation qui rendrait plus fluide le déplacement.

## Conclusion

Ce projet a été très enrichissant sur plusieurs aspects. Il nous a permis de mettre en pratique chaque semaine ce que nous avions appris la semaine d’avant en automatique ou en programmation. Cela nous a permis d’approfondir également nos connaissances en robotique et de voir les problématiques liées à l’implémentation numérique de correcteurs. Il est à noter que notre stage de deuxième année sera dans la continuité de ce travail car nous l’effectuerons au sein de l’IMS en collaboration avec Rhoban.

## GLOSSAIRE

Consigne : vitesse souhaitée du moteur.

Commande : tension réelle envoyée au moteur.

Dépassement : dépassement de la vitesse du moteur par rapport à sa valeur en régime permanent (valeur finale).

Direct Driving : les moteurs déplacent le robot sans passer par une réduction mécanique.

Erreur statique : erreur de vitesse entre celle souhaitée et celle atteinte.

Gain statique : coefficient entre la valeur atteinte par le moteur en régime permanent et la commande qui lui a été appliquée.

Perturbation : événement imprévu agissant sur le moteur (bruit de mesure, frottements supplémentaires, etc..).

Procédé : correspond dans notre cas au moteur et à toute la chaîne de traitement analogique et numérique. C’est la boite noire que l’on cherche à contrôler.

Pseudo-pulsation : pulsation liée aux dépassements successifs de la vitesse autour de sa valeur finale.

Temps de montée : temps pris par le moteur pour aller de 10% à 90% de sa vitesse finale.

## Bibliographie

- “PID control of brushless DC motor and robot trajectory planning and simulation with Matlab/Simulink” --- Oludayo John Oguntoyinbo – 2009
- “Dynamical Models for Omni-directional Robots with 3 and 4 Wheels” – Helder P. Oliveira, Armando Jorge Sousa, A. Paulo Moreira, Paulo José Cerqueira Gomes da Costa – 2008
- Datasheet of Maxon EC45 70W flat
